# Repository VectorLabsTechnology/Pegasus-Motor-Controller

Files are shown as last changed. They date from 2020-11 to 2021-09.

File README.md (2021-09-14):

# Pegasus Motor Controller

## Objetivo

O objetivo do projeto é desenvolver um inversor para um motor síncrono de ímãs permanentes utilizando a técnica de controle orientado a campo. Com isso, se espera obter a familiaridadee com tecnologias modernas de controle de motores, tendo como objetivo final desenvolver um inversor capaz de acionar motores trifásicos e BLDC.

## Especificações

Em primeira instância, o motor a ser acionado será um motor oriundo de um _hoverboard_, brushless sensorado, operando a 48V e com potência máxima de 2,2kW. Com base nesses aprendizados, espera-se no futuro ser possível acionarmos um motor de maior tensão e potência, já de fabricação própria. As especificações técnicas mais específicas podem ser encontradas na [CT-001](/docs/CT-001-Especificacoes-Gerais.md).

## Organização do projeto

O repositório está dividido em quatro subdiretórios, `docs`, `fw`, `hw` e `sw`, que contêm respectivamente a documentação, firmware, hardware e software do projeto.
A parte de documentação é organizada majoritariamente no formato de [CTs](/docs/README.md). O design de hardware está sendo realizado com a ferramenta KiCad.

## Renders of the borads
Power Electronics:
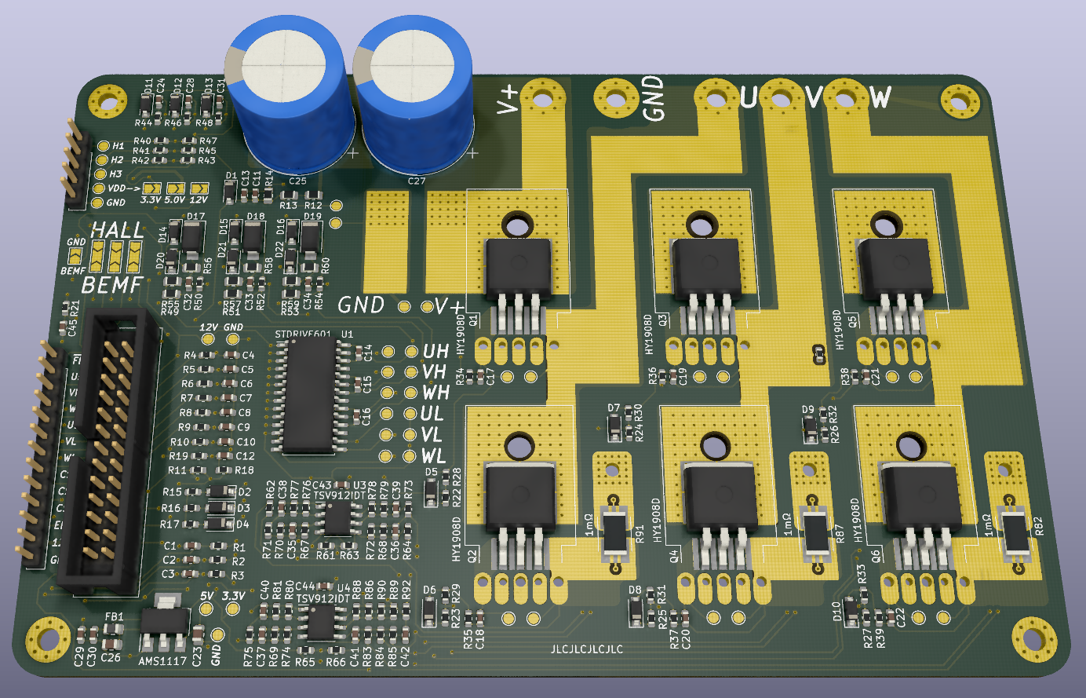
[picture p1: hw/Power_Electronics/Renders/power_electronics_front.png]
Power Electronics 1


Control Board:
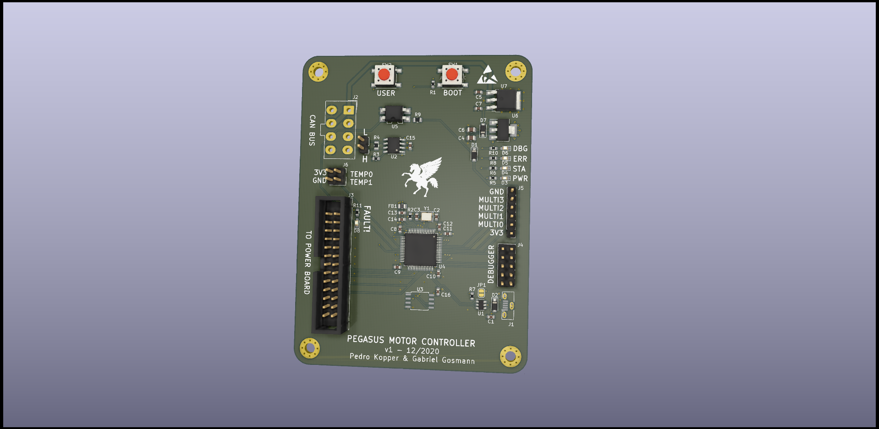
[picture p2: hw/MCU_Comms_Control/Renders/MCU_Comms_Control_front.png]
Control


Video of the test on a 3-phase induction motor
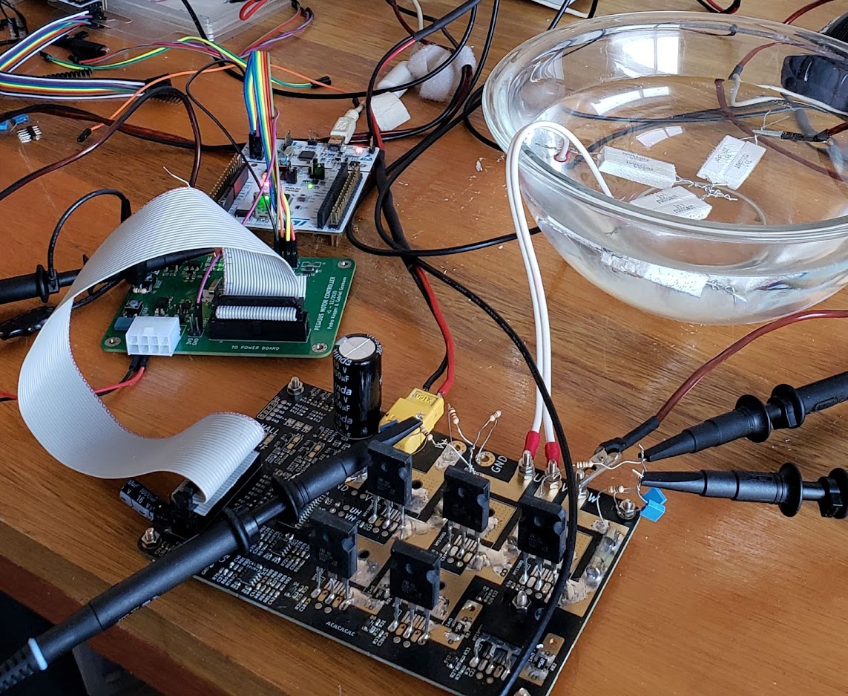
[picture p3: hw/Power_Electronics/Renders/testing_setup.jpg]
Watch the video (https://www.youtube.com/watch?v=kWv3p37wL9I&t=134s)


### Licença

O projeto está licenciado sob a licença MIT. Isso quer dizer que você tem o direto de reproduzir ele, tanto o software quanto o hardware.

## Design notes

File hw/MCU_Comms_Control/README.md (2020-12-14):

# Placa de controle

---

Placa renderizada frente

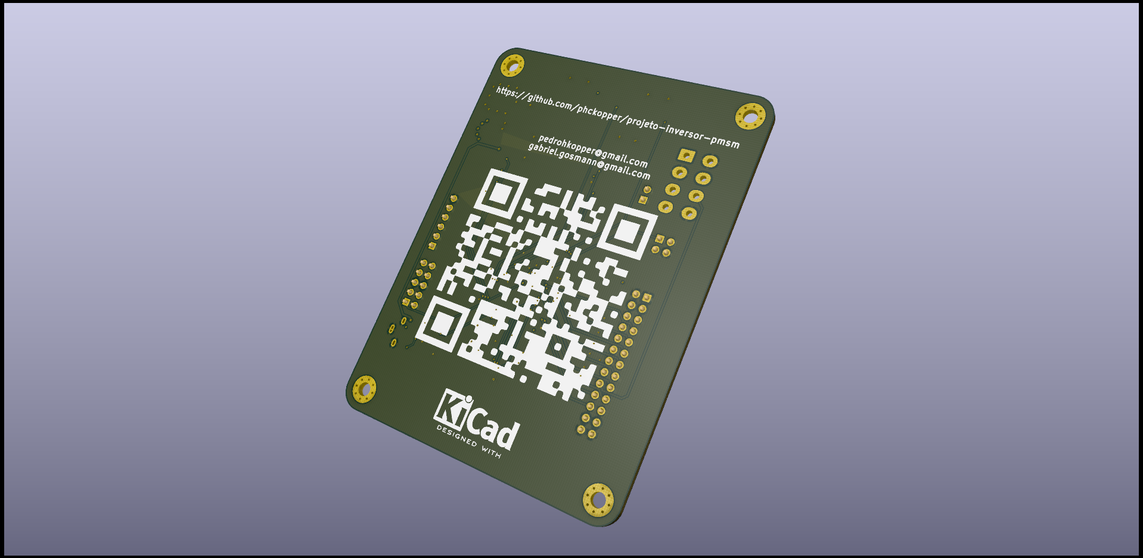
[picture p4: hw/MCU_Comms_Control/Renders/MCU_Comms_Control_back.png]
Placa renderizada trás


---

Essa placa é responsável por realizar o acionamento e controle dos motores. Utilizando um STM32F303, ela é capaz de medir a corrente ou força eletromotriz reversa de cada fase, possibilitando a comutação das bobinas. Além disso, possui entradas para sensores Hall, permitindo o uso de motores sensorados. 

Além do acionamento do motor, a placa realiza a comunicação com o resto do carro via barramento CAN, possibilitando o ajuste remoto de torque. Também possui uma entrada para o barramento de falha do carro, que desativa automaticamente a saída em caso de pane em qualquer um dos sistemas. Entradas para termistores permitem o monitoramento contínuo da temperatura da ponte do inversor, possibilitando o desarme em caso de sobreaquecimento. O monitoramento da tensão da bateria permite que as saídas sejam desligadas em caso de sobre/subtensão.

Com fim de telemetria, a placa conta com uma memória flash de 128Mbits, que pode ser lida através de conexão USB para possibilitar a caracterização da performance do inveersor e do motor, diagnosticar panes, entre outros.

---

Esse design é hardware livre e é disponibilizado através da licença CERN-OHL-S v2 (fortemente recíproca), disponível em inglês [aqui](https://ohwr.org/cern_ohl_s_v2.txt).

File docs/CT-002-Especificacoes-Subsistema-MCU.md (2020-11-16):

# [CT-001] Especificações do subsistema microcontrolado

**Escopo:** MCU e demais partes do controle eletrônico
**Objetivo:** Detalhar as especificações e a escolha dos componentes para a parte de controle microeletrônico

### Das especificações

O sistema microcontrolado deverá ser capaz de:

- [ ] Executar o algoritmo de controle orientado a campo especificado na [CT-001](/docs/CT-001-Especificacoes-Gerais.md) na frequência especificada, preferencialmente com o uso de uma FPU
- [ ] Realizar a amostragem do sinal das três correntes com frequência igual ou superior à frequência do algoritmo de controle orientado a campo, com a maior resolução possível
- [ ] Emitir seis saídas PWM, sendo elas três pares complementares, com frequência de chaveamento igual ou superior à especificada na CT-001.
- [ ] Ler três sensores de efeito Hall digitais com velocidade compatível com a especificação
- [ ] Possuir, preferencialmente, periférico CAN integrado suportando a especificação 2.0B a uma velocidade igual ou superior a 500kbps
- [ ] Possuir, preferencialmente, periférico SPI para possibilitar a adição da memória flash
- [ ] Possuir, preferencialmente, periférico USB para possibilitar uma interface de configuração e atualização de firmware em campo

### Das escolhas

Para cumprir as especificações anteriores, iniciamos pesquisando microcontroladores da fabricante ST, patrocinadora da e-Power e de conhecimento dos autores. Nisso, limitamos nosso espaço de escolha para a linha STM32.

Dentro das linhas STM32, existem diversas linhas, mas focaremos nas G0, G4, F0, F1 e F3, que são as consideradas para uso "mainstream". Dentre elas, a linha G é a mais recente, porém por conta disso possui disponibilidade muito limitada no mercado chinês no momento da escrita desse documento. Ficamos então com as linhas F1 e F3. Dentre elas, escolhemos a linha F3 por dois motivos principais:

* Impossibilidade de utilizar o periférico CAN ao mesmo tempo que o USB na linha F1, devido ao compartilhamento da SRAM
* Maior disponibilidade de periféricos analógicos na linha F3 (comparadores rápidos e amplificadores operacionais)

Dentro da linha F3, optamos pelo STM32F303 pois era o microcontrolador com maior disponibilidade e menor custo na LCSC/JLCPCB em novembro/2020. [Datasheet](https://www.st.com/resource/en/datasheet/stm32f303cc.pdf). O encapsulamento e número de pinos será estabelecido próximo ao término do design, porém os passos iniciais serão dados com a versão LQFP48.

### Do processamento

O STM32F303 é implementado em cima da arquitetura ARM Cortex-M4, voltada para alta performance e com suporte a ponto flutuante em hardware, o que facilita a escrita do algoritmo. Além disso, possui um controlador DMA de 12 canais, permitindo realizar diversas operações de movimentação de dados sem utilizar a CPU. Também possui uma MPU, que pode ser interessante para aumentar a segurança do firmware.

### Do conversor analógico digital (ADC)

O STM32F303 possui quatro ADCs, capazes de operar até 5Msps e multiplexados em até 39 canais, dependendo do encapsulamento escolhido. Sua resolução é programável até 12 bits e possibilita amostragem de 0V a 3.6V. Além disso, possui quatro PGAs integrados que possibilitam um ganho de 2x, 4x, 8x ou 16x, com entrada e saída rail-to-rail e largura de banda de 8.2MHz.

### Dos timers de controle do motor

O STM32F303 possui dois timers avançados (TIM1 e TIM8) que podem ser utilizados como PWM trifásico multiplexado em seis canais, com saídas complementares e dead-time programável. Esses timers também podem funcionar em conjunto com outros para realizar a sincronização de eventos dentro da MCU, por exemplo, de amostragem do conversor ADC.

### Das entradas de efeito Hall

O STM32F303 possui até 87 pinos de GPIO, sendo eles tolerantes a entradas de 5V, mesmo quando operando com Vcc = 3.3V. Todos eles são mapeados em vetores de interrupção externos e alguns podem ser conectados à timers para decodificação em quadratura via hardware.

### Do periférico CAN

O STM32F303 possui um periférico CAN que adere à espeecificação CAN2.0B e suporta velocidades de até 1Mbps e endereçamento de 29 bits.

### Do periférico SPI

O STM32F303 possui um periférico SPI que pode ser utilizado para interfacear tanto com memória flash quanto com cartões SD

### Do periférico USB

O STM32F303 possui um periférico USB compatível com a especificação full-speed (12Mbps), com SRAM dedicada para os buffers de transmissão e recepção. Para seu uso é necessário utilizar um cristal externo a partir do HSE.

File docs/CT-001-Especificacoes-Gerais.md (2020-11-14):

# [CT-001] Especificações gerais do projeto

**Escopo:** Todos subsistemas
**Objetivo:** Detalhar de maneira granular as especificações que devem ser cumpridas pelo projeto.

### Da etapa de potência

Deve ser capaz de:

- [ ] Ser alimentada por uma tensão de 36V a 48V
- [ ] Suportar uma corrente de 50A em regime contínuo
- [ ] Ser tolerante à picos de 150% do regime contínuo
- [ ] Desarmar caso uma sobrecorrente de 150% aconteça, só podedendo ser rearmado manualmente via botão ou CAN
- [ ] Permitir a leitura da corrente de pelo menos três fases separadamente
- [ ] Permitir a leitura da tensão de cada fase individualmente
- [ ] Permitir a leitura da tensão de alimentação
- [ ] Permitir a leitura da temperatura média dos MOSFETs da ponte
- [ ] Permitir um chaveamento de, no mínimo, 20 kHz

### Da parte microcontrolada

Deve ser capaz de:

- [ ] Ser alimentado através de uma fonte externa de 5V-24V
- [ ] Operar a partir de um barramento de 3.3V
- [ ] Consumir, no máximo, 100mA
- [ ] Medir a corrente das fases disponíveis e calcular as demais via software
- [ ] Realizar o controle orientado a campo das saídas
- [ ] Estimar a posição do rotor através de três entradas para sensores de efeito Hall
- [ ] Possuir saídas PWM capazes de acionar os gate drivers
- [ ] Monitorar condições de falha da etapa de potência, entrando em modo de erro caso necessário (sobrecorrente, sobretemperatura e violação das Leis de Kirchoff)
- [ ] Receber comandos de setpoint do torque via barramento CAN
- [ ] Responder, quando indagado via CAN, a velocidade, a corrente e a tensão do motor
- [ ] Armazenar em memória flash continuamente os parâmetros operacionais do motor, bem como o estado do software

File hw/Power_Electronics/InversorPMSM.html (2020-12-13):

# /home/phckopper/Projects/projeto-inversor-pmsm/hw/Power_Electronics/InversorPMSM.sch

sex 04 dez 2020 16:39:09

Eeschema 5.1.6

Component Count:178

Ref | Qnty | Value | Part | Datasheet | Description | Vendor
C1, C2, C3, C4, C5, C6, C32, C33, C34, C38 | 10 | 33pF | Device:C | Samsung-Electro-Mechanics-CL10C330JB8NNNC_C1663.pdf | Unpolarized capacitor
C7, C8, C26, C27, C40, C41 | 6 | 100nF | Device:C | ~ | Unpolarized capacitor
C9, C13, C14, C15, C16, C17, C18 | 7 | DNM | Device:C | | Unpolarized capacitor
C10, C11, C12 | 3 | 470nF | Device:C | Samsung-Electro-Mechanics-CL10B474KA8NNNC_C1623.pdf | Unpolarized capacitor
C19, C22 | 2 | 22uF | Device:C | ~ | Unpolarized capacitor
C20, C25, C28, C29, C30, C31, C35, C36, C37 | 9 | 10pF | Device:C | Samsung-Electro-Mechanics-CL10C330JB8NNNC_C1663.pdf | Unpolarized capacitor
C21 | 1 | CP | Device:CP | ~ | Polarized capacitor
C23 | 1 | CP | Device:CP | ~ | Polarized capacitor
C24 | 1 | DNM | Device:C | ~ | Unpolarized capacitor
C39 | 1 | 1nF | Device:C | ~ | Unpolarized capacitor
D1, D5, D6, D7, D8, D9, D10, D11, D12, D13, D14, D15, D16, D20, D21, D22 | 16 | B5819W | Device:D_Schottky | Changjiang-Electronics-Tech-CJ-B5819W_C8598.pdf | Schottky diode
D2, D3, D4 | 3 | DNM | Device:D_Schottky | | Schottky diode
D17, D18, D19 | 3 | RS1J | Device:D | ~ | Diode
FB1 | 1 | Ferrite | Device:Ferrite_Bead | ~ | Ferrite bead
H1, H2, H3, H4 | 4 | MountingHole_Pad | Mechanical:MountingHole_Pad | ~ | Mounting Hole with connection
J1 | 1 | FROM_CONTROL_BOARD | Connector_Generic:Conn_02x13_Odd_Even | ~ | Generic connector, double row, 02x13, odd/even pin numbering scheme (row 1 odd numbers, row 2 even numbers), script generated (kicad-library-utils/schlib/autogen/connector/)
J2 | 1 | HALL_CONNECTOR | Connector:Conn_01x05_Male | ~ | Generic connector, single row, 01x05, script generated (kicad-library-utils/schlib/autogen/connector/)
J3 | 1 | POWER_INPUT | Connector:Screw_Terminal_01x02 | ~ | Generic screw terminal, single row, 01x02, script generated (kicad-library-utils/schlib/autogen/connector/)
J4 | 1 | OUTPUT POWER | Connector:Screw_Terminal_01x03 | ~ | Generic screw terminal, single row, 01x03, script generated (kicad-library-utils/schlib/autogen/connector/)
JP1, JP2, JP3 | 3 | Jumper_2_Open | Jumper:Jumper_2_Open | ~ | Jumper, 2-pole, open
JP4, JP5, JP6 | 3 | Jumper_3_Open | Jumper:Jumper_3_Open | ~ | Jumper, 3-pole, both open
Q1, Q2, Q3, Q4, Q5, Q6 | 6 | HY1908D | Transistor_FET:IRF3205 | https://datasheet.lcsc.com/szlcsc/1809071509_HUAYI-HY1908D_C108891.pdf | 110A Id, 55V Vds, Single N-Channel HEXFET Power MOSFET, 8mOhm Ron, TO-220AB
Q7, Q8, Q9, Q10, Q11, Q12 | 6 | JCS24N50WH | Transistor_FET:IRF3205 | | 110A Id, 55V Vds, Single N-Channel HEXFET Power MOSFET, 8mOhm Ron, TO-220AB
R1, R2, R3, R4, R5, R6, R42, R44, R46, R75, R76, R77, R78 | 13 | 1K | Device:R | Uniroyal-Elec-0603WAF1001T5E_C21190.pdf | Resistor
R7, R26, R27, R28, R29, R30, R31, R53, R55, R57, R59, R60, R61, R68, R69, R70, R71, R72, R73 | 19 | 100K | Device:R | Uniroyal-Elec-0603WAF1003T5E_C25803.pdf | Resistor
R8, R9, R41, R43, R45, R47, R49, R51 | 8 | 100K | Device:R | | Resistor
R10, R48, R50, R52 | 4 | 5.6K | Device:R | | Resistor
R11, R12, R13 | 3 | 27R | Device:R | | Resistor
R14, R15, R16, R17, R18, R19 | 6 | 10R | Device:R | https://datasheet.lcsc.com/szlcsc/Uniroyal-Elec-0603WAF100JT5E_C22859.pdf | Resistor
R20, R21, R22, R23, R24, R25 | 6 | 100R | Device:R | Uniroyal-Elec-0603WAF1000T5E_C22775.pdf | Resistor
R32, R33, R34, R54, R56, R58, R63, R65, R67 | 9 | 2K | Device:R | Uniroyal-Elec-0603WAF1001T5E_C21190.pdf | Resistor
R35, R37, R39, R84 | 4 | 10K | Device:R | | Resistor
R36, R38, R40, R62, R64, R66, R80, R82 | 8 | DNM | Device:R | Uniroyal-Elec-0603WAF1001T5E_C21190.pdf | Resistor
R74, R79, R83 | 3 | 1mΩ | Device:R | ~ | Resistor
R81 | 1 | 39K | Device:R | Uniroyal-Elec-0603WAF1003T5E_C25803.pdf | Resistor
U1 | 1 | STDRIVE601 | inversor-pmsm:STDRIVE601 | https://www.st.com/resource/en/datasheet/stdrive601.pdf | Triple half-bridge high-voltage gate driver
U2 | 1 | AMS1117 | Regulator_Linear:AMS1117 | http://www.advanced-monolithic.com/pdf/ds1117.pdf | 1A Low Dropout regulator, positive, adjustable output, SOT-223
U3, U4 | 2 | TSV912IDT | Amplifier_Operational:TSV912IDT | www.st.com/resource/en/datasheet/tsv911.pdf | Dual rail-to-rail input/output 8 MHz operational amplifiers, SOIC-8

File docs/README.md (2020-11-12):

# Documentação do projeto

Nesse diretório estão contidas as CTs (Considerações Técnicas) realizadas durante o desenvolvimento do projeto. O objetivo delas é documentar o processo decisório realizado durante o design do inversor, e não somente o resultado final.

As CTs devem ser escrita no formato Markdown (.md) e seguir o seguinte formato:

```
# [CT-xxx] [Título descritivo (eg. Estimação da dissipação de potência nos MOSFETs)]

*Escopo:* [Quais subsistemas são considerados nessa CT (eg. MOSFETs da ponte)]
*Objetivo:* [Descrever de maneira mais precisa o conteúdo da CT]

[Corpo]
```

O objetivo de adotar o sistema de CTs é permitir que as decisões de design sejam documentadas de maneira consistente e, assim, o projeto se torne verificável por terceiros e facilite a inclusão de novos membros na equipe, além de facilitar o surgimento de adaptações e outros trabalhos derivativos.

O link entre CTs é encorajado e, sempre que for possível, tente linkar no corpo para as CTs que contém as informações que você referencia.

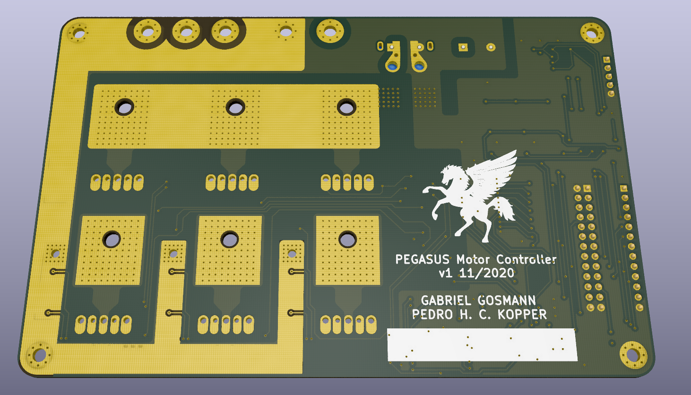
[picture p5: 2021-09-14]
hw/Power_Electronics/Renders/power_electronics_back.png

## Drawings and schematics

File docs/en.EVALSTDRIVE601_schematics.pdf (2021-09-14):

### HIGH VOLTAGE SECTION

### VCC_E min 9V max 20V

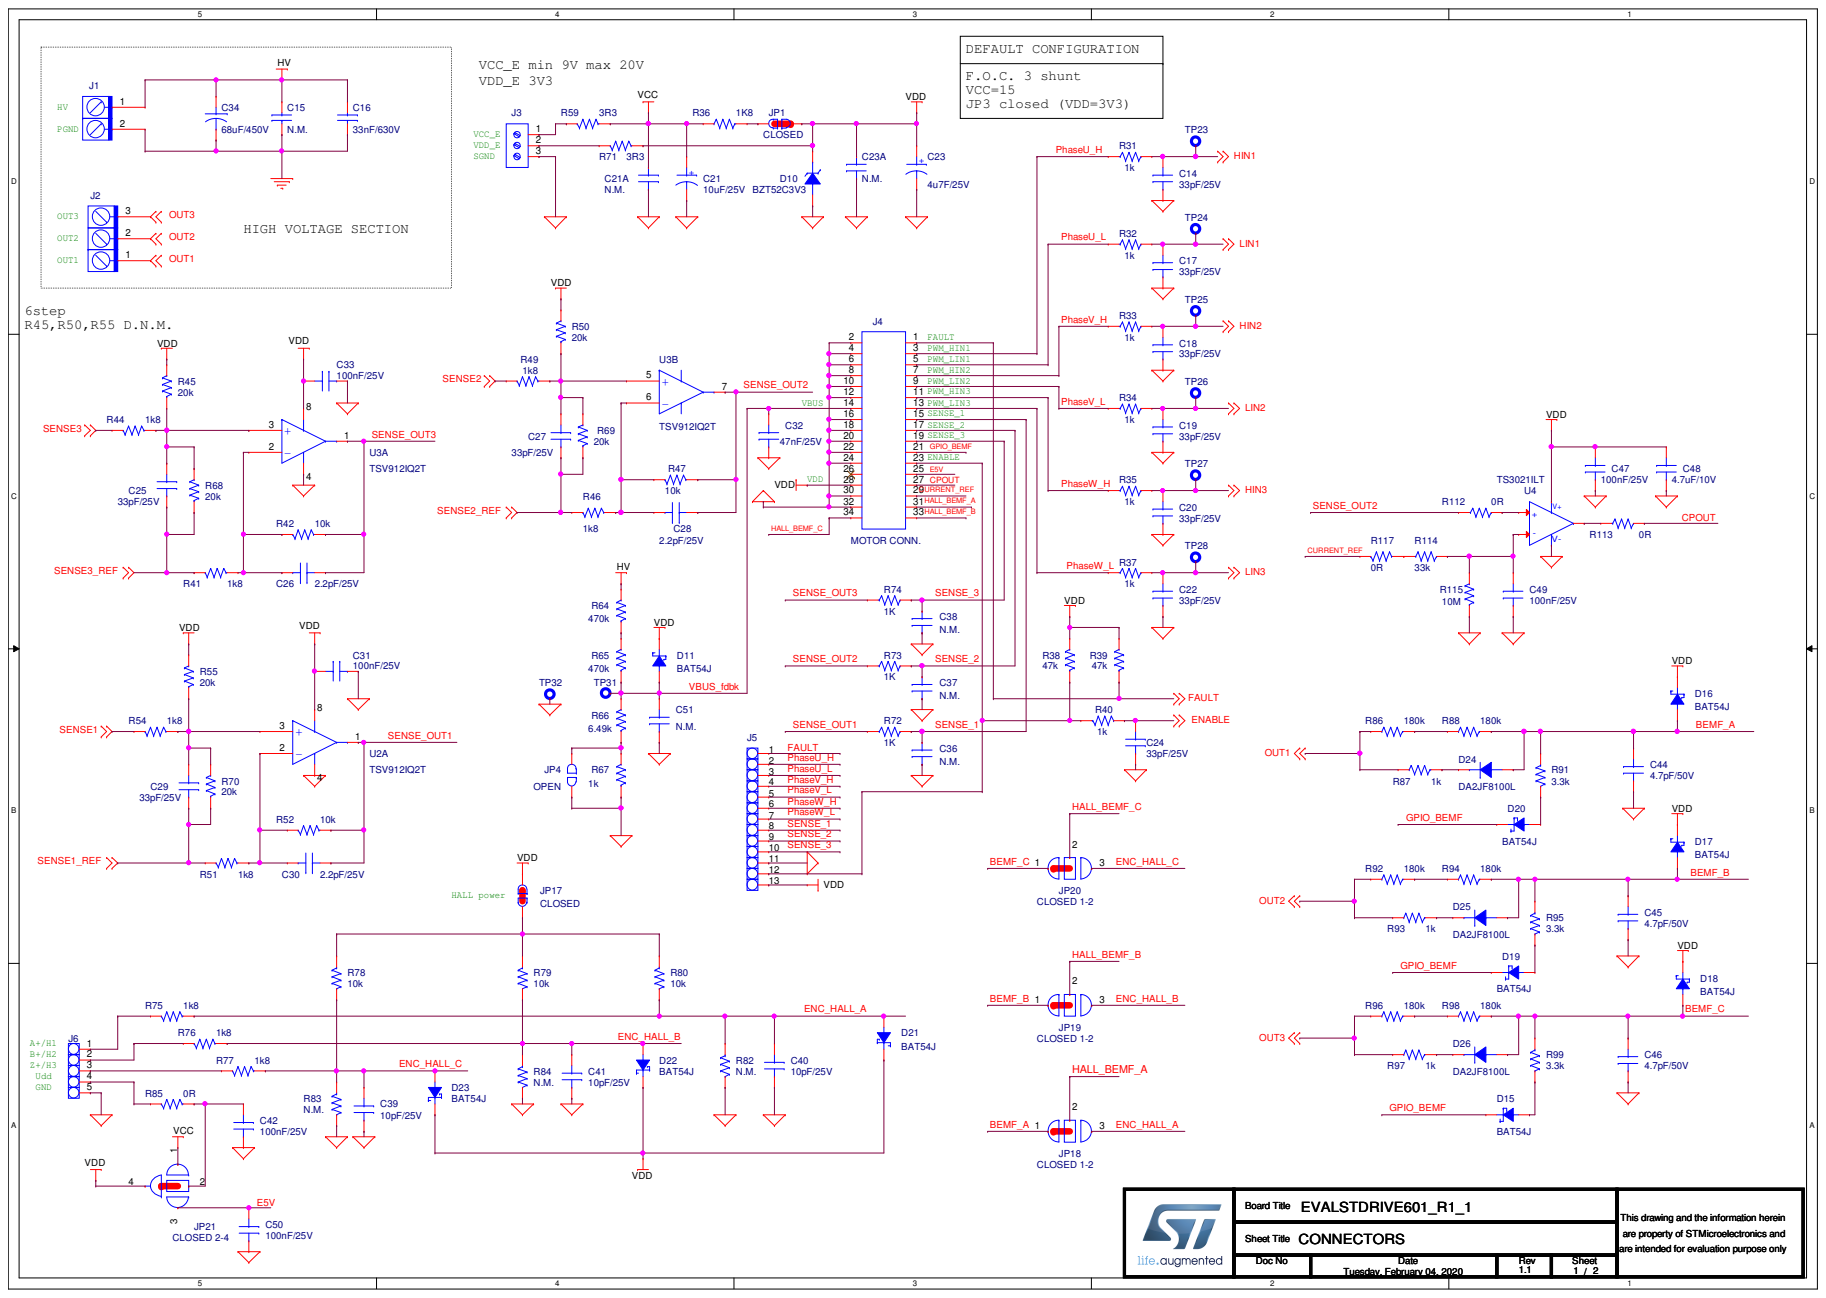
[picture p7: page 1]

This drawing and the information herein
are property of STMicroelectronics and
are intended for evaluation purpose only

HV

SGND | PGND

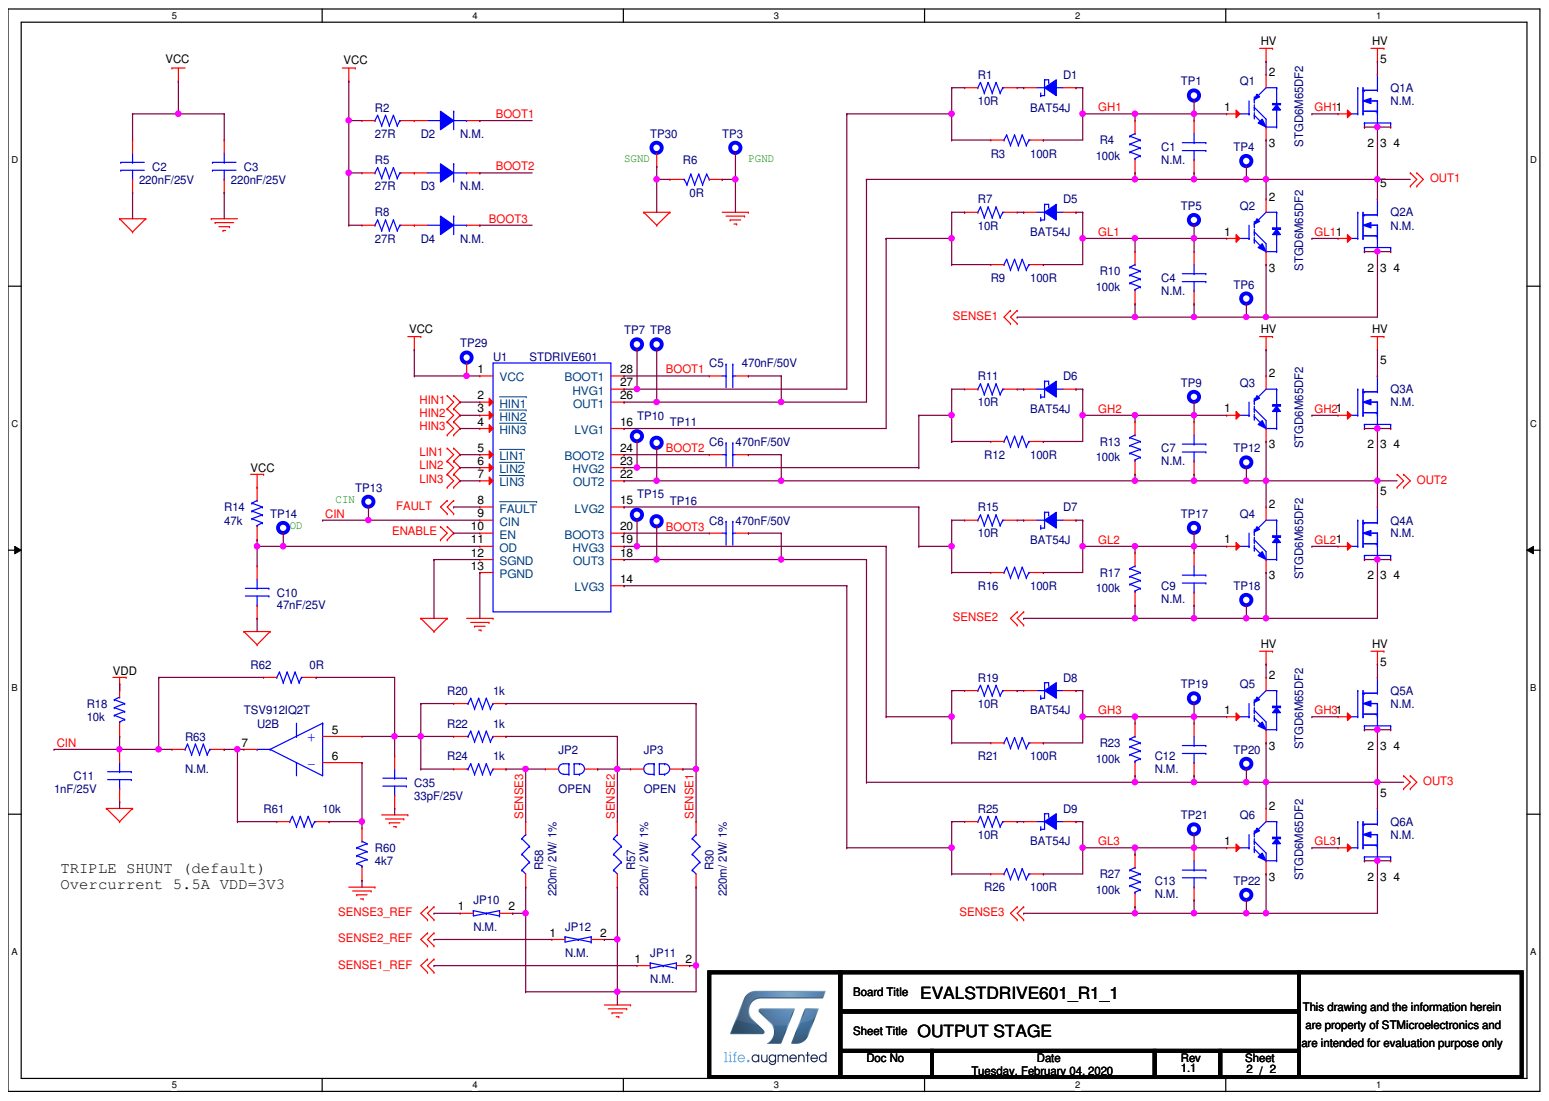
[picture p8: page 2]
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

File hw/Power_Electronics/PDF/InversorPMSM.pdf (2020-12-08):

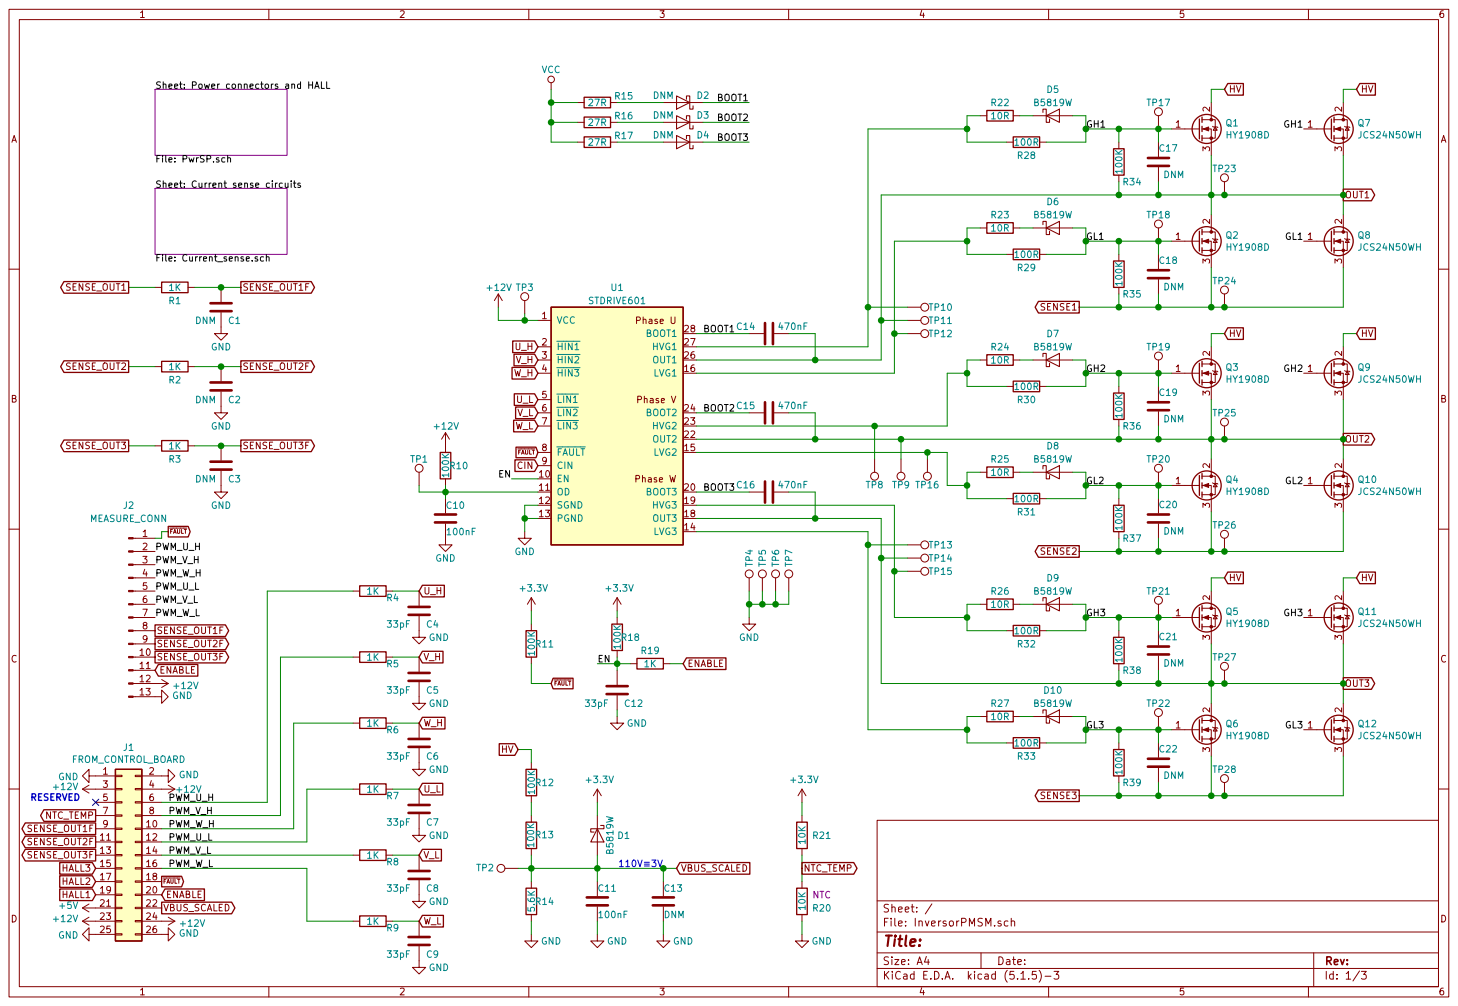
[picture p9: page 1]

Sheet: Power connectors and HALL File: PwrSP.sch Sheet: Current sense circuits File: Current_sense.sch

Id: 1/3 Title: File: InversorPMSM.sch Sheet: /

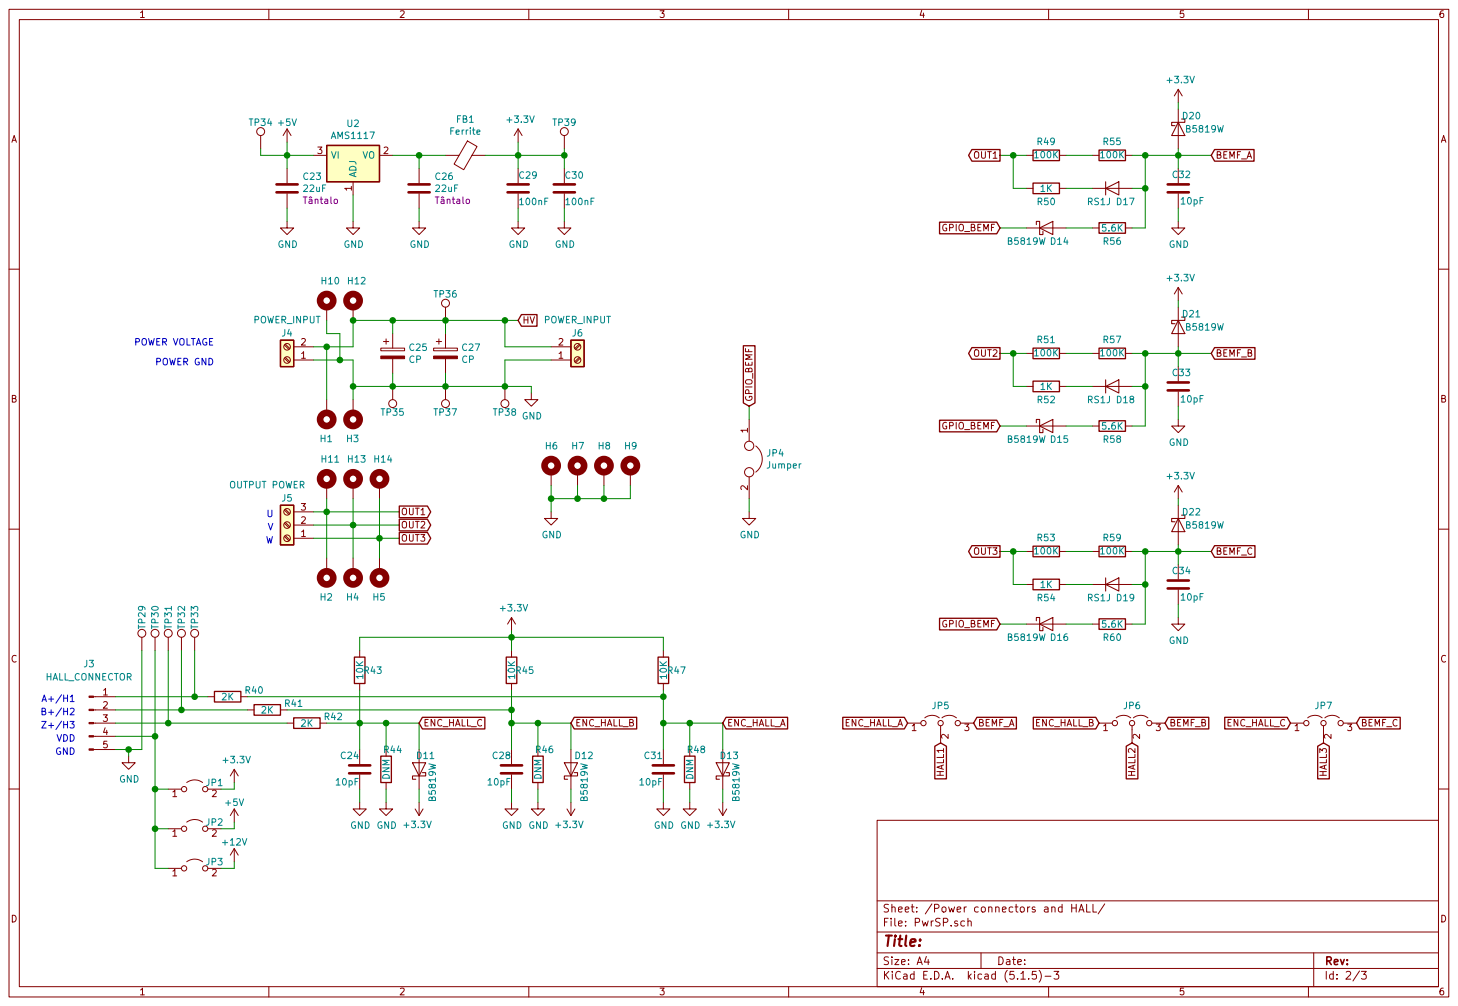
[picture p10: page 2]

Id: 2/3 Title: File: PwrSP.sch Sheet: /Power connectors and HALL/ +12V

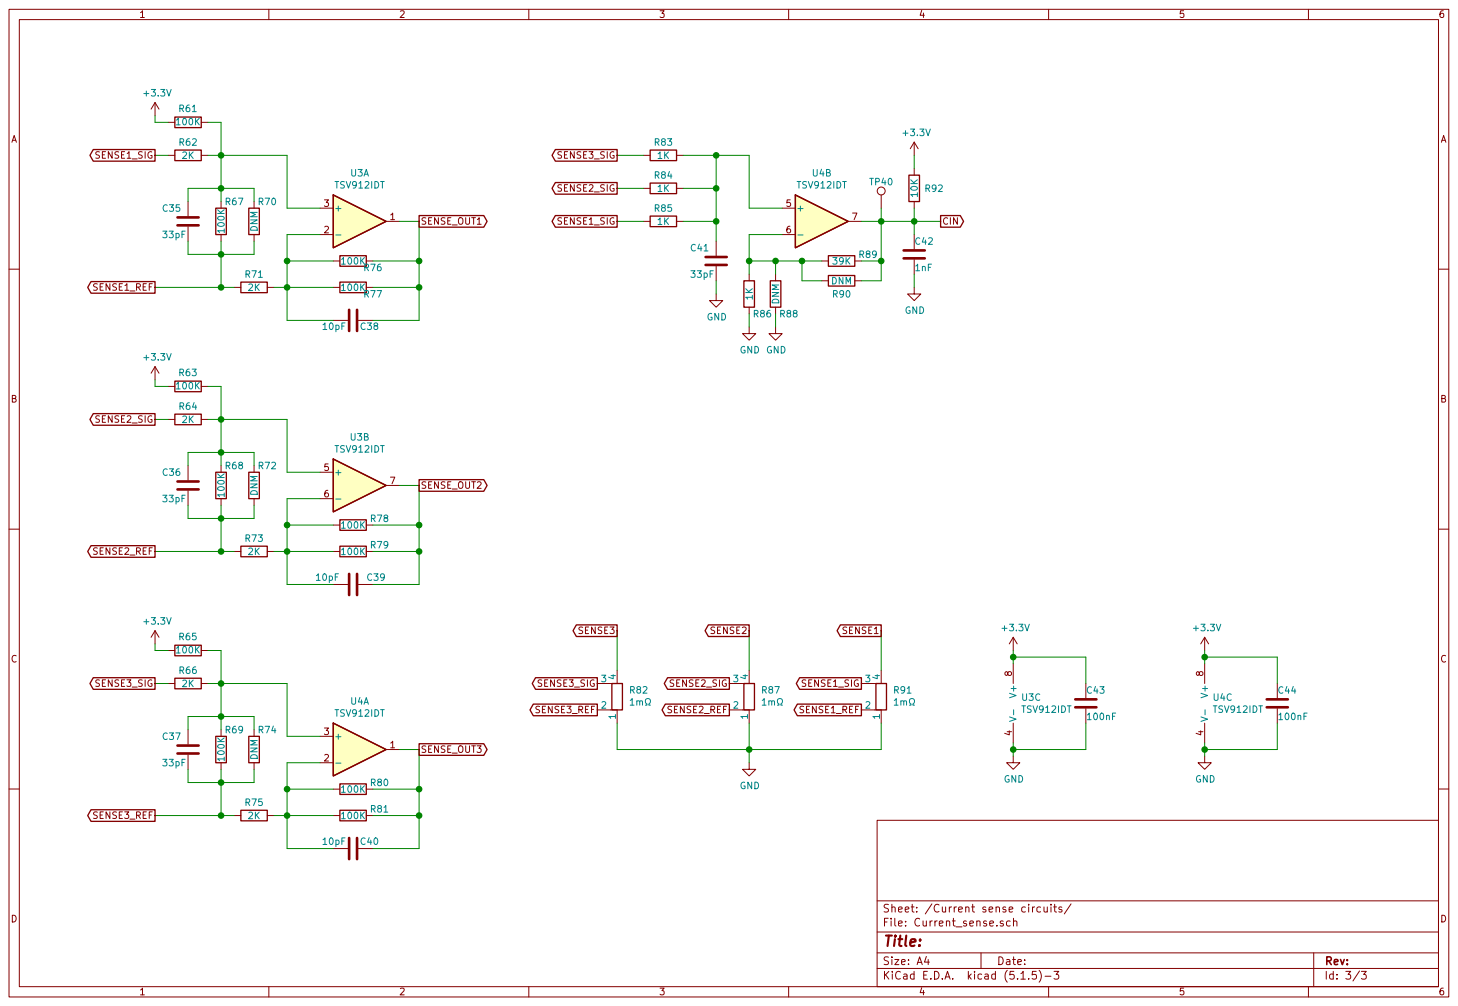
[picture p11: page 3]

File: Current_sense.sch Sheet: /Current sense circuits/ R72 DNM

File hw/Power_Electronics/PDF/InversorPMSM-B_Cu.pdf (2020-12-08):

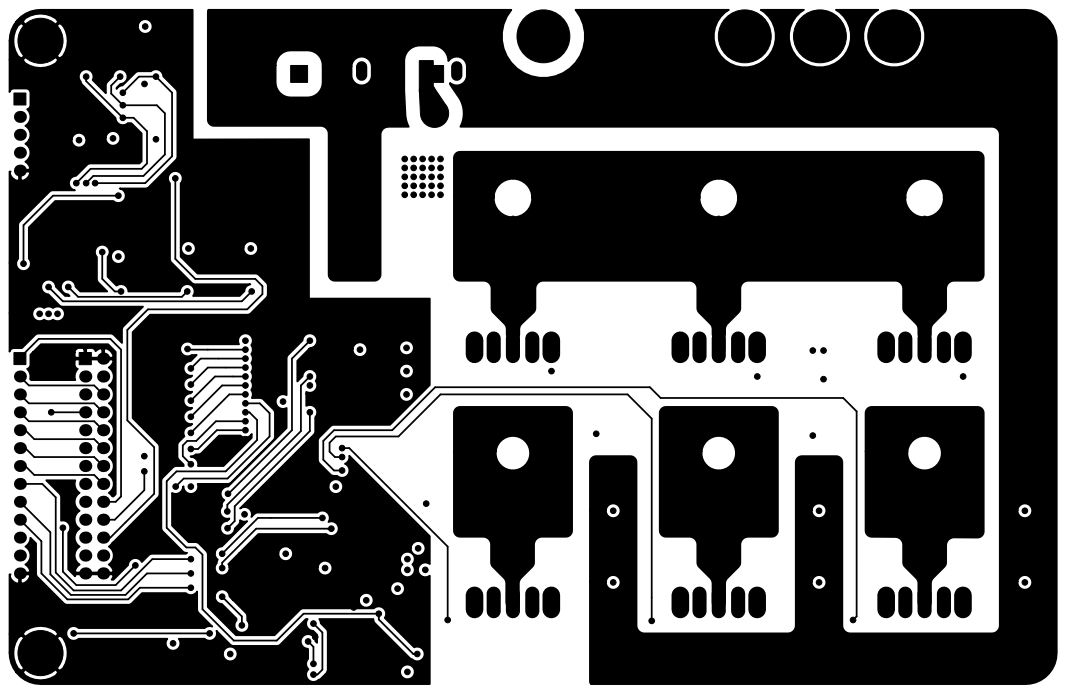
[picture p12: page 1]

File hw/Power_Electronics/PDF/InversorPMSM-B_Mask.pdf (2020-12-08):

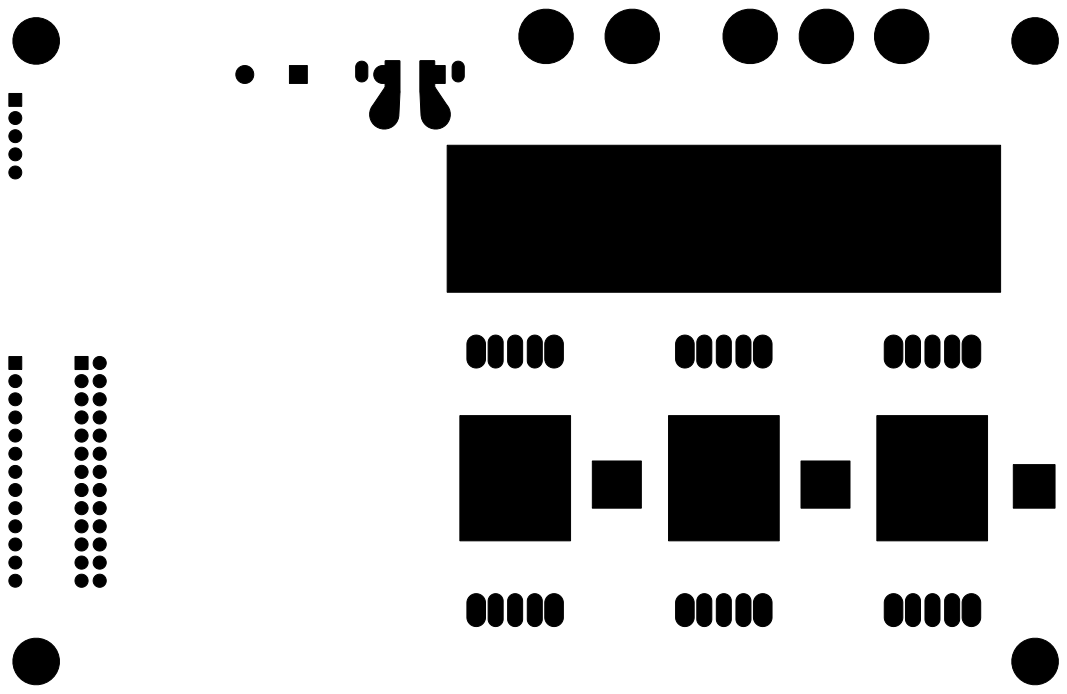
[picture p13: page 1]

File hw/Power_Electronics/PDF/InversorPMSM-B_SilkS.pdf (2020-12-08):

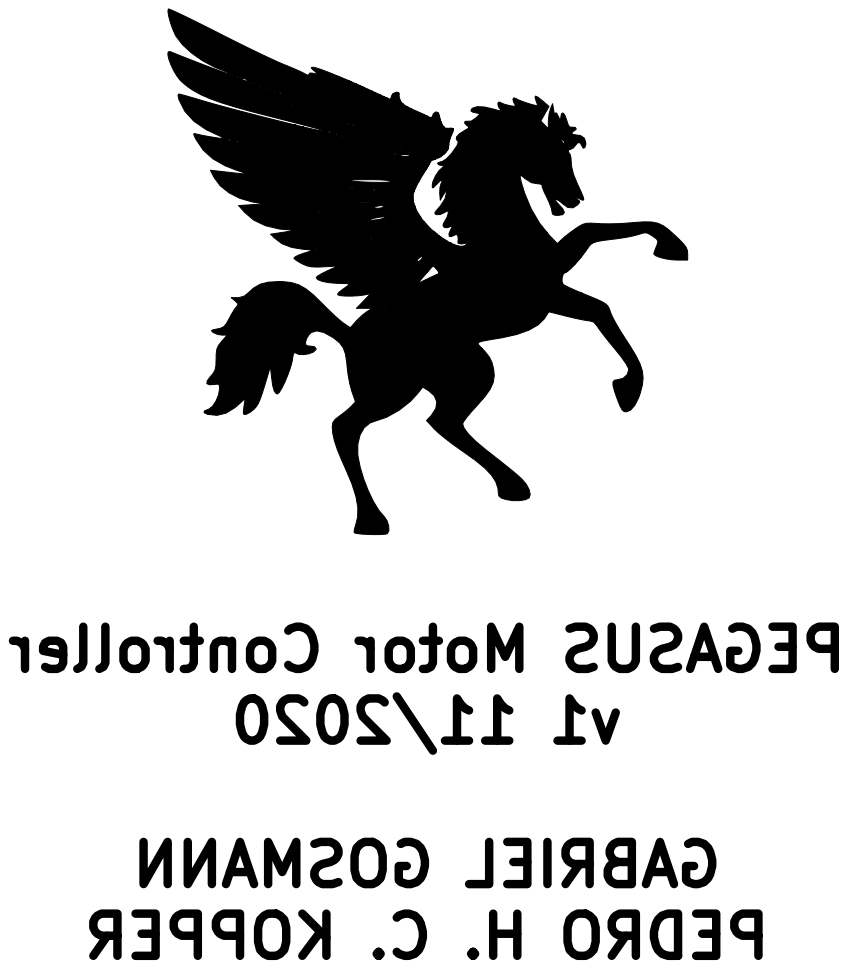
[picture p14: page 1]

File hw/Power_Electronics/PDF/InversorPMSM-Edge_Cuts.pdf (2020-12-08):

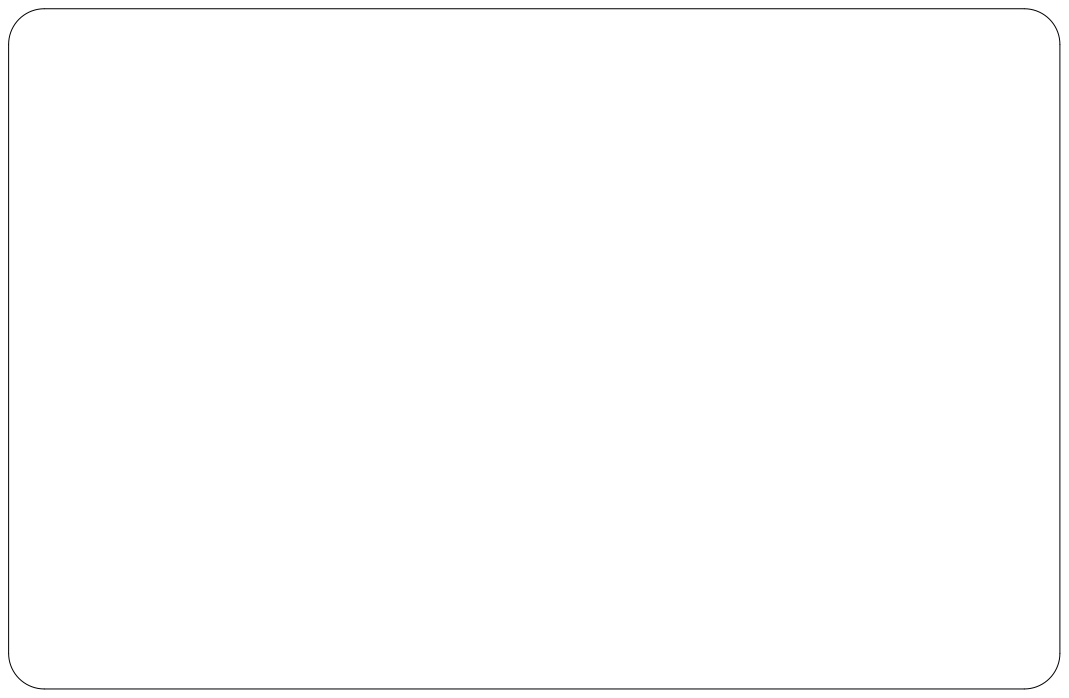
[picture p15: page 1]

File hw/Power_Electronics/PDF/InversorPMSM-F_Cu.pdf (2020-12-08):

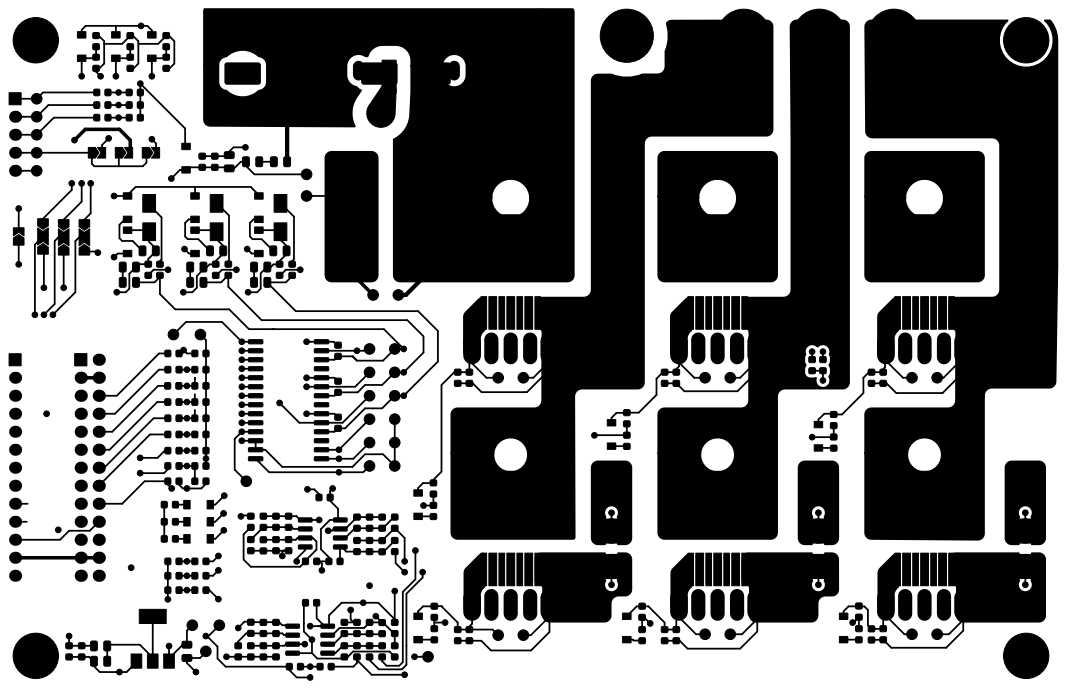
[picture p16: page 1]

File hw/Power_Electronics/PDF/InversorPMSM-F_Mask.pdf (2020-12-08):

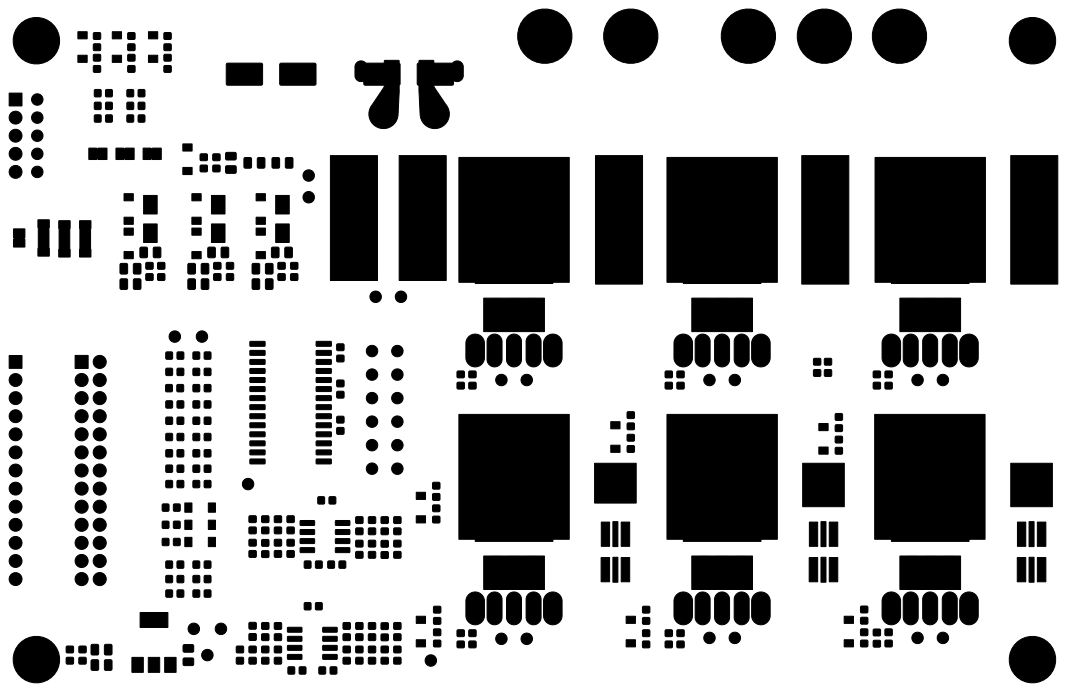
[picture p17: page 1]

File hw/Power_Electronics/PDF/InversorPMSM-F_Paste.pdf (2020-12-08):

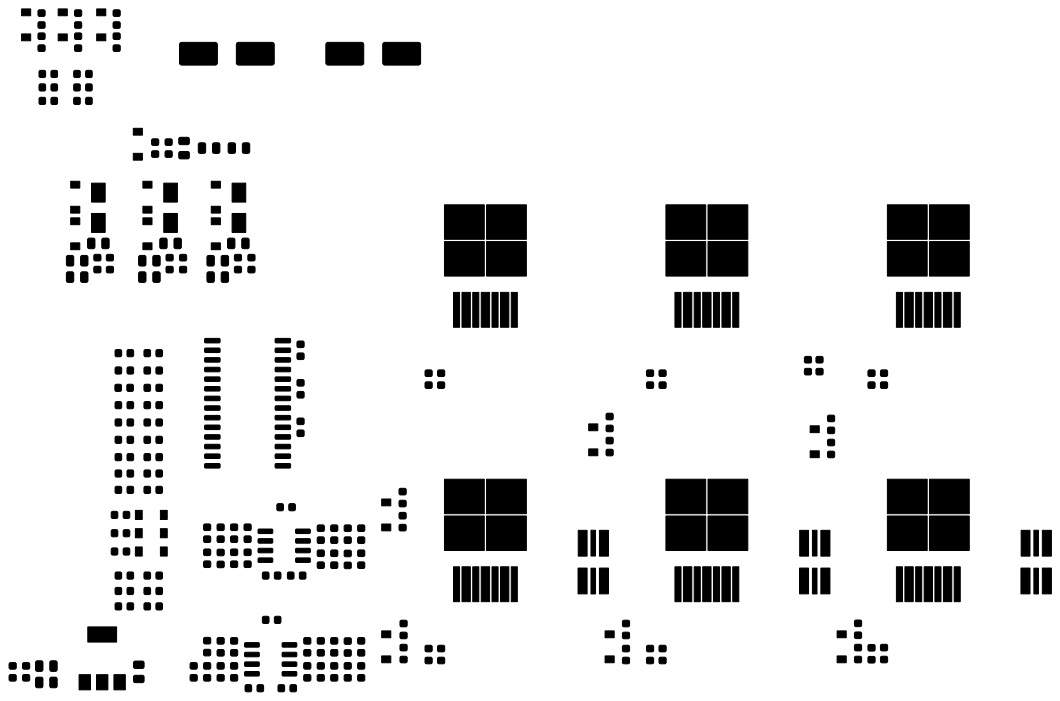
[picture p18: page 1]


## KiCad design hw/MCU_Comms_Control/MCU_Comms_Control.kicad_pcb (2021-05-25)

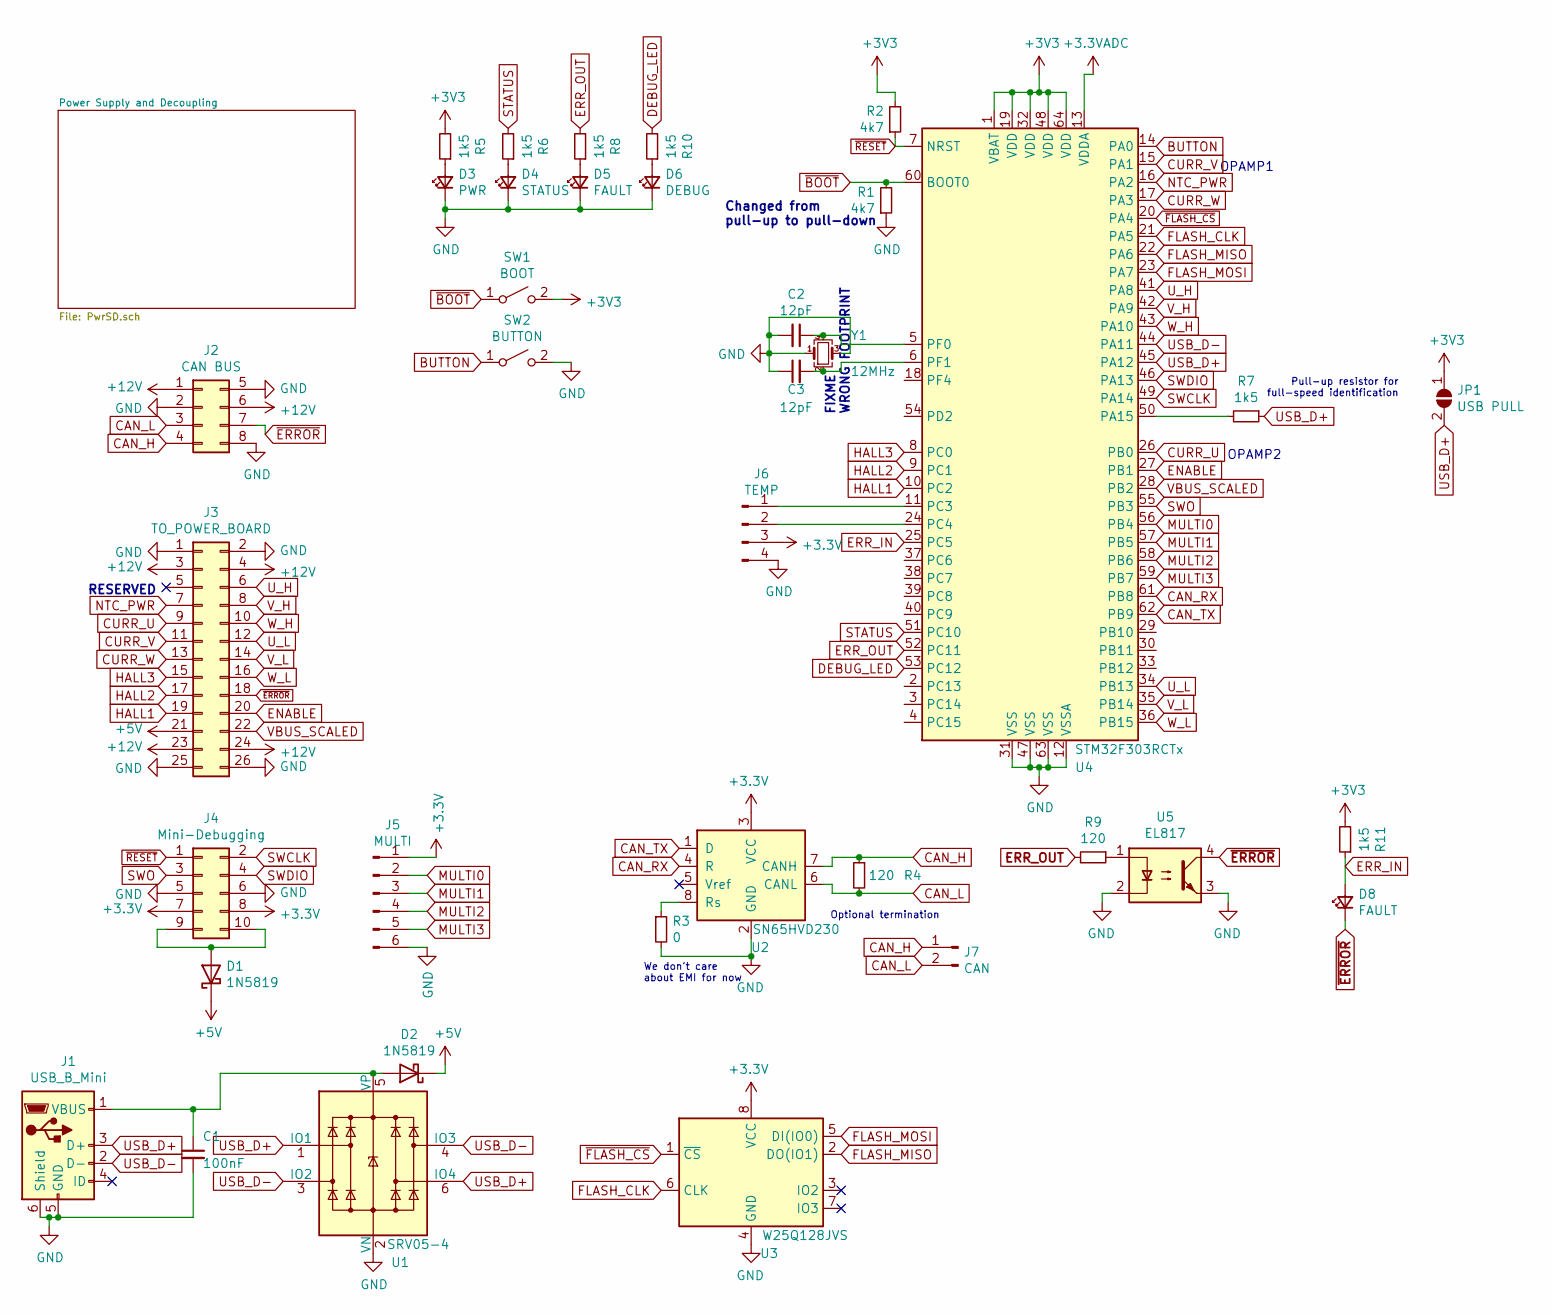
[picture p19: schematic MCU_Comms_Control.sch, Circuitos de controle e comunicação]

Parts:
C1: 100nF; C_0603_1608Metric; LCSC C14663
C2, C3: 12pF; C_0603_1608Metric; LCSC C38523
D1, D2: 1N5819; D_SOD-123; LCSC C8598
D3: PWR; LED_0603_1608Metric_Castellated; LCSC C72043
D4: STATUS; LED_0603_1608Metric_Castellated; LCSC C72041
D5, D8: FAULT; LED_0603_1608Metric_Castellated; LCSC C2286
D6: DEBUG; LED_0603_1608Metric_Castellated; LCSC C72041
J1: USB_B_Mini; USB_Micro-B_Molex-105133-0001
J2: CAN BUS; Molex_Mini-Fit_Jr_5566-08A_2x04_P4.20mm_Vertical
J3: TO_POWER_BOARD; IDC-Header_2x13_P2.54mm_Vertical
J4: Mini-Debugging; PinHeader_2x05_P2.54mm_Vertical
J5: MULTI; PinHeader_1x06_P2.54mm_Vertical
J6: TEMP; PinHeader_2x02_P2.54mm_Vertical
J7: CAN; PinHeader_1x02_P2.54mm_Vertical
JP1: USB PULL; SolderJumper-2_P1.3mm_Open_RoundedPad1.0x1.5mm
R1, R2: 4k7; R_0603_1608Metric; LCSC C23162
R3: 0; R_0603_1608Metric; LCSC C21189
R4, R9: 120; R_0805_2012Metric; LCSC C17437
R5, R6, R7, R8, R10, R11: 1k5; R_0603_1608Metric; LCSC C22843
SW1: BOOT; SW_SPST_PTS645
SW2: BUTTON; SW_SPST_PTS645
U1: SRV05-4; SOT-23-6; LCSC C85364
U2: SN65HVD230; SOIC-8_3.9x4.9mm_P1.27mm; LCSC C12084
U3: W25Q128JVS; SOIC-8_5.23x5.23mm_P1.27mm; LCSC C97521
U4: STM32F303RCTx; LQFP-64_10x10mm_P0.5mm
U5: EL817; SMDIP-4_W7.62mm; LCSC C106900
Y1: 12MHz; Crystal_SMD_3225-4Pin_3.2x2.5mm; LCSC C9002

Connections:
+3.3VADC: U4.13 (VDDA); also elsewhere on the board
+5V: D1.1 (K), D2.1 (K), J3.21; also elsewhere on the board
+12V: J2.1, J2.6, J3.3, J3.4, J3.23, J3.24; also elsewhere on the board
BUTTON: SW2.1 (A), U4.14 (PA0)
CAN_H: J2.4, J7.1, R4.1, U2.7 (CANH)
CAN_L: J2.3, J7.2, R4.2, U2.6 (CANL)
CAN_RX: U2.4 (R), U4.61 (PB8)
CAN_TX: U2.1 (D), U4.62 (PB9)
CURR_U: J3.9, U4.26 (PB0)
CURR_V: J3.11, U4.15 (PA1)
CURR_W: J3.13, U4.17 (PA3)
DEBUG_LED: R10.2, U4.53 (PC12)
ENABLE: J3.20, U4.27 (PB1)
ERR_IN: D8.2 (A), R11.1, U4.25 (PC5)
ERR_OUT: R8.2, R9.2, U4.52 (PC11)
FLASH_CLK: U3.6 (CLK), U4.21 (PA5)
FLASH_MISO: U3.2 (DO(IO1)), U4.22 (PA6)
FLASH_MOSI: U3.5 (DI(IO0)), U4.23 (PA7)
GND: C1.2, C2.2, C3.1, D3.1 (K), D4.1 (K), D5.1 (K), D6.1 (K), J1.5 (GND), J1.6 (Shield), J2.2, J2.5, J2.8, J3.1, J3.2, J3.25, J3.26, J4.5, J4.6, J5.6, J6.4, R1.1, R3.2, SW2.2 (B), U1.2 (VN), U2.2 (GND), U3.4 (GND), U4.12 (VSSA), U4.31 (VSS), U4.47 (VSS), U4.63 (VSS), U5.2, U5.3, Y1.1, Y1.3; also elsewhere on the board
HALL1: J3.19, U4.10 (PC2)
HALL2: J3.17, U4.9 (PC1)
HALL3: J3.15, U4.8 (PC0)
MULTI0: J5.2, U4.56 (PB4)
MULTI1: J5.3, U4.57 (PB5)
MULTI2: J5.4, U4.58 (PB6)
MULTI3: J5.5, U4.59 (PB7)
NTC_PWR: J3.7, U4.16 (PA2)
unnamed: C1.1, D2.2 (A), J1.1 (VBUS), U1.5 (VP)
unnamed: C2.1, U4.5 (PF0), Y1.4
unnamed: C3.2, U4.6 (PF1), Y1.2
unnamed: D1.2 (A), J4.9, J4.10
unnamed: D3.2 (A), R5.1
unnamed: D4.2 (A), R6.1
unnamed: D5.2 (A), R8.1
unnamed: D6.2 (A), R10.1
unnamed: J6.1, U4.11 (PC3)
unnamed: J6.2, U4.24 (PC4)
unnamed: R3.1, U2.8 (Rs)
unnamed: R7.2, U4.50 (PA15)
unnamed: R9.1, U5.1
STATUS: R6.2, U4.51 (PC10)
SWCLK: J4.2, U4.49 (PA14)
SWDIO: J4.4, U4.46 (PA13)
SWO: J4.3, U4.55 (PB3)
USB_D+: J1.3 (D+), JP1.2 (B), R7.1, U1.1 (IO1), U1.6 (IO4), U4.45 (PA12)
USB_D-: J1.2 (D-), U1.3 (IO2), U1.4 (IO3), U4.44 (PA11)
U_H: J3.6, U4.41 (PA8)
U_L: J3.12, U4.34 (PB13)
VBUS_SCALED: J3.22, U4.28 (PB2)
V_H: J3.8, U4.42 (PA9)
V_L: J3.14, U4.35 (PB14)
W_H: J3.10, U4.43 (PA10)
W_L: J3.16, U4.36 (PB15)
~BOOT: R1.2, SW1.1 (A), U4.60 (BOOT0)
~ERROR: D8.1 (K), J2.7, J3.18, U5.4
~FLASH_CS: U3.1 (~CS), U4.20 (PA4)
~RESET: J4.1, R2.1, U4.7 (NRST)

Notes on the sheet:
Optional termination
We don't care about EMI for now
Pull-up resistor for full-speed identification
RESERVED
OPAMP1
OPAMP2
Changed from pull-up to pull-down
FIXME WRONG FOOTPRINT

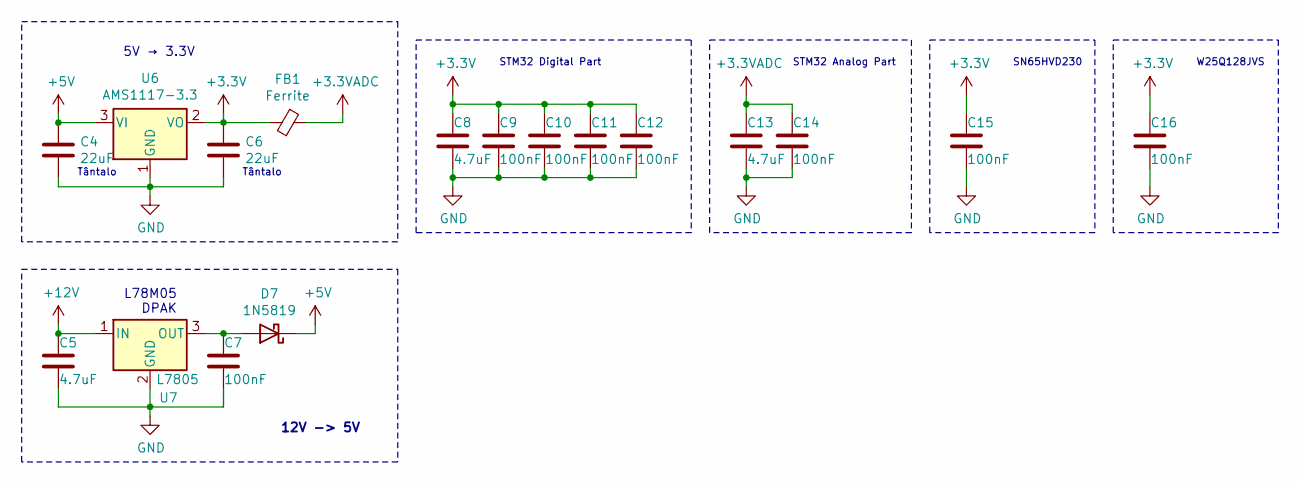
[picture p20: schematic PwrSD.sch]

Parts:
C4, C6: 22uF; C_0805_2012Metric; LCSC C45783
C5, C8, C13: 4.7uF; C_0603_1608Metric; LCSC C19666
C7, C9, C10, C11, C12, C14, C15, C16: 100nF; C_0603_1608Metric; LCSC C14663
D7: 1N5819; D_SOD-123; LCSC C8598
FB1: Ferrite; L_0805_2012Metric; LCSC e
U6: AMS1117-3.3; SOT-223-3_TabPin2; LCSC C6186
U7: L7805; TO-252-3_TabPin2; LCSC C58069

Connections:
+3.3VADC: C13.1, C14.1, FB1.1; also elsewhere on the board
+5V: C4.1, D7.1 (K), U6.3 (VI); also elsewhere on the board
+12V: C5.1, U7.1 (IN); also elsewhere on the board
GND: C4.2, C5.2, C6.2, C7.2, C8.2, C9.2, C10.2, C11.2, C12.2, C13.2, C14.2, C15.2, C16.2, U6.1 (GND), U7.2 (GND); also elsewhere on the board
unnamed: C7.1, D7.2 (A), U7.3 (OUT)

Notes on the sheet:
Tântalo
STM32 Digital Part
STM32 Analog Part
5V → 3.3V
SN65HVD230
W25Q128JVS
L78M05 DPAK
12V -> 5V

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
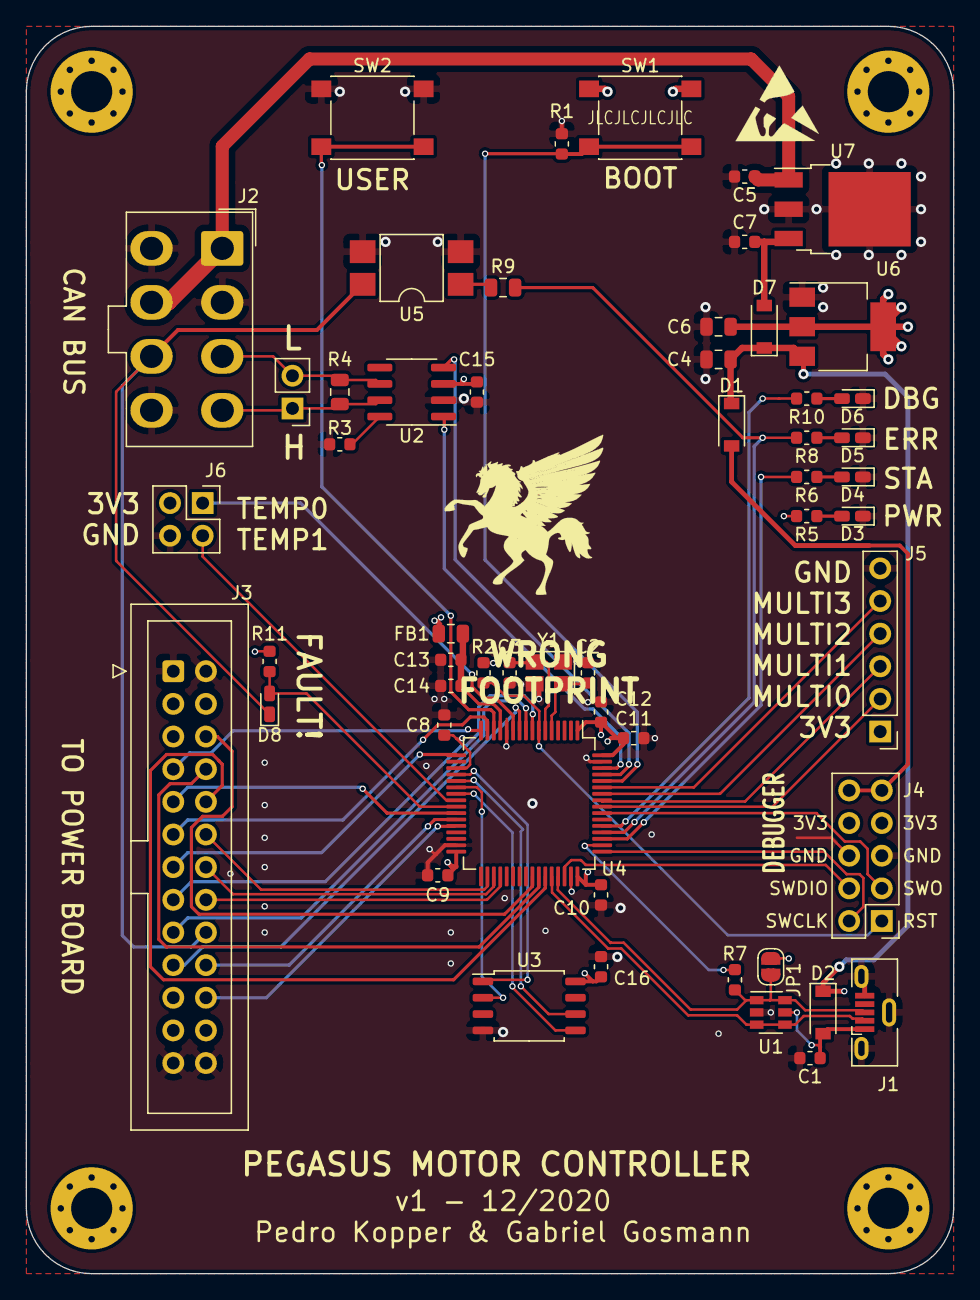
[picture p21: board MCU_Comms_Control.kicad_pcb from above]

Board: 4 copper layers, 72.1 x 97.0 mm, 54 parts (0 on the bottom side), 59 nets.

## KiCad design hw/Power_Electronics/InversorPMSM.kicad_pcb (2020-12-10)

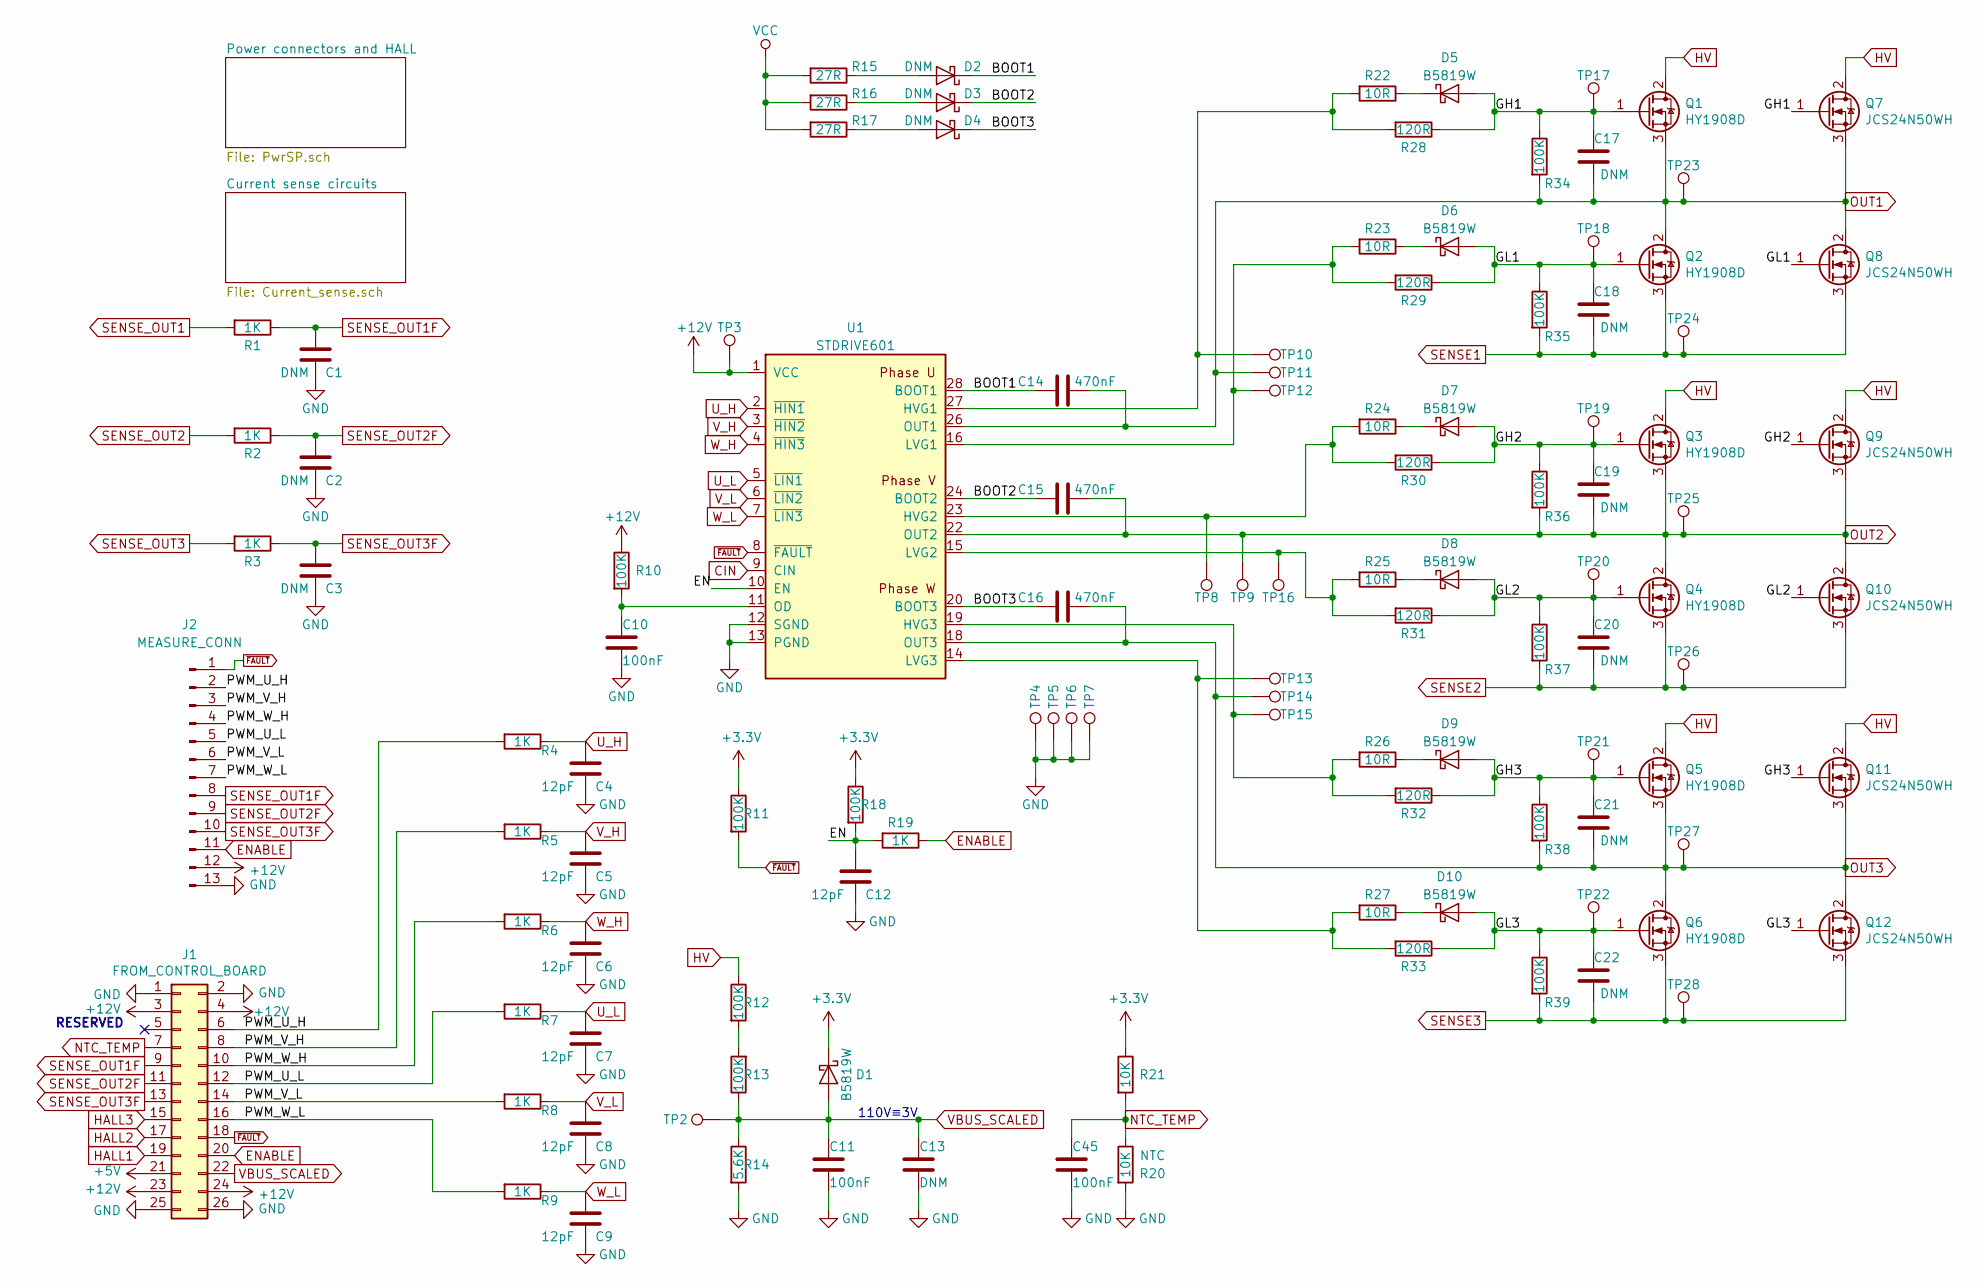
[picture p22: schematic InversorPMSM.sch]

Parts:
C1, C2, C3, C13, C17, C18, C19, C20, C21, C22: DNM; C_0603_1608Metric
C4, C5, C6, C7, C8, C9, C12: 12pF; C_0603_1608Metric; LCSC C38523
C10, C11, C45: 100nF; C_0603_1608Metric; LCSC C14663
C14, C15, C16: 470nF; C_0603_1608Metric; LCSC C1623
D1, D5, D6, D7, D8, D9, D10: B5819W; D_SOD-123; LCSC C8598
D2, D3, D4: DNM; D_SOD-123
J1: FROM_CONTROL_BOARD; IDC-Header_2x13_P2.54mm_Vertical
J2: MEASURE_CONN; PinHeader_1x13_P2.54mm_Vertical
Q1, Q2, Q3, Q4, Q5, Q6: HY1908D; Universal_MOSFET_generic
Q7, Q8, Q9, Q10, Q11, Q12: JCS24N50WH
R1, R2, R3, R4, R5, R6, R7, R8, R9, R19: 1K; R_0603_1608Metric; LCSC C21190
R10, R11, R18, R34, R35, R36, R37, R38, R39: 100K; R_0603_1608Metric; LCSC C25803
R12, R13: 100K; R_0805_2012Metric; LCSC C17407
R14: 5.6K; R_0805_2012Metric; LCSC C4382
R15, R16, R17: 27R; R_0603_1608Metric; LCSC C25190
R20: 10K; R_0603_1608Metric; LCSC C13564
R21: 10K; R_0603_1608Metric; LCSC C25804
R22, R23, R24, R25, R26, R27: 10R; R_0603_1608Metric; LCSC C22859
R28, R29, R30, R31, R32, R33: 120R; R_0603_1608Metric; LCSC C17437
TP2, TP3, TP4, TP5, TP6, TP7, TP8, TP9, TP10, TP11, TP12, TP13, TP14, TP15, TP16, TP17, TP18, TP19, TP20, TP21, TP22, TP23, TP24, TP25, TP26, TP27, TP28: TestPoint; TestPoint_Pad_D1.5mm
U1: STDRIVE601; SOIC-28W_7.5x17.9mm_P1.27mm

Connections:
+3V3: D1.1 (K), R11.1, R18.1, R21.1; also elsewhere on the board
+5V: J1.21; also elsewhere on the board
+12V: J1.3, J1.4, J1.23, J1.24, J2.12, R10.1, TP3.1, U1.1 (VCC); also elsewhere on the board
/BOOT1: C14.1, D2.1 (K), U1.28 (BOOT1)
/BOOT2: C15.1, D3.1 (K), U1.24 (BOOT2)
/BOOT3: C16.1, D4.1 (K), U1.20 (BOOT3)
/EN: C12.1, R18.2, R19.2, U1.10 (EN)
/GH1: C17.2, D5.2 (A), Q1.1 (G), Q7.1 (G), R28.1, R34.1, TP17.1
/GH2: C19.2, D7.2 (A), Q3.1 (G), Q9.1 (G), R30.1, R36.1, TP19.1
/GH3: C21.2, D9.2 (A), Q5.1 (G), Q11.1 (G), R32.1, R38.1, TP21.1
/GL1: C18.2, D6.2 (A), Q2.1 (G), Q8.1 (G), R29.1, R35.1, TP18.1
/GL2: C20.2, D8.2 (A), Q4.1 (G), Q10.1 (G), R31.1, R37.1, TP20.1
/GL3: C22.2, D10.2 (A), Q6.1 (G), Q12.1 (G), R33.1, R39.1, TP22.1
/PWM_U_H: J1.6, J2.2, R4.2
/PWM_U_L: J1.12, J2.5, R7.2
/PWM_V_H: J1.8, J2.3, R5.2
/PWM_V_L: J1.14, J2.6, R8.2
/PWM_W_H: J1.10, J2.4, R6.2
/PWM_W_L: J1.16, J2.7, R9.2
CIN: U1.9 (CIN); also elsewhere on the board
ENABLE: J1.20, J2.11, R19.1
GND: C1.2, C2.2, C3.2, C4.2, C5.2, C6.2, C7.2, C8.2, C9.2, C10.2, C11.2, C12.2, C13.2, C45.2, J1.1, J1.2, J1.25, J1.26, J2.13, R14.2, R20.2, TP4.1, TP5.1, TP6.1, TP7.1, U1.12 (SGND), U1.13 (PGND); also elsewhere on the board
HALL1: J1.19; also elsewhere on the board
HALL2: J1.17; also elsewhere on the board
HALL3: J1.15; also elsewhere on the board
HV: Q1.2 (D), Q3.2 (D), Q5.2 (D), Q7.2 (D), Q9.2 (D), Q11.2 (D), R12.1; also elsewhere on the board
NTC_TEMP: C45.1, J1.7, R20.1, R21.2
unnamed: C10.1, R10.2, U1.11 (OD)
unnamed: D2.2 (A), R15.1
unnamed: D3.2 (A), R16.1
unnamed: D4.2 (A), R17.1
unnamed: D5.1 (K), R22.1
unnamed: D6.1 (K), R23.1
unnamed: D7.1 (K), R24.1
unnamed: D8.1 (K), R25.1
unnamed: D9.1 (K), R26.1
unnamed: D10.1 (K), R27.1
unnamed: R12.2, R13.2
unnamed: R22.2, R28.2, TP10.1, U1.27 (HVG1)
unnamed: R23.2, R29.2, TP12.1, U1.16 (LVG1)
unnamed: R24.2, R30.2, TP8.1, U1.23 (HVG2)
unnamed: R25.2, R31.2, TP16.1, U1.15 (LVG2)
unnamed: R26.2, R32.2, TP15.1, U1.19 (HVG3)
unnamed: R27.2, R33.2, TP13.1, U1.14 (LVG3)
OUT1: C14.2, C17.1, Q1.3 (S), Q2.2 (D), Q7.3 (S), Q8.2 (D), R34.2, TP11.1, TP23.1, U1.26 (OUT1); also elsewhere on the board
OUT2: C15.2, C19.1, Q3.3 (S), Q4.2 (D), Q9.3 (S), Q10.2 (D), R36.2, TP9.1, TP25.1, U1.22 (OUT2); also elsewhere on the board
OUT3: C16.2, C21.1, Q5.3 (S), Q6.2 (D), Q11.3 (S), Q12.2 (D), R38.2, TP14.1, TP27.1, U1.18 (OUT3); also elsewhere on the board
SENSE1: C18.1, Q2.3 (S), Q8.3 (S), R35.2, TP24.1; also elsewhere on the board
SENSE2: C20.1, Q4.3 (S), Q10.3 (S), R37.2, TP26.1; also elsewhere on the board
SENSE3: C22.1, Q6.3 (S), Q12.3 (S), R39.2, TP28.1; also elsewhere on the board
SENSE_OUT1: R1.2; also elsewhere on the board
SENSE_OUT1F: C1.1, J1.9, J2.8, R1.1
SENSE_OUT2: R2.2; also elsewhere on the board
SENSE_OUT2F: C2.1, J1.11, J2.9, R2.1
SENSE_OUT3: R3.2; also elsewhere on the board
SENSE_OUT3F: C3.1, J1.13, J2.10, R3.1
U_H: C4.1, R4.1, U1.2 (~HIN1)
U_L: C7.1, R7.1, U1.5 (~LIN1)
VBUS_SCALED: C11.1, C13.1, D1.2 (A), J1.22, R13.1, R14.1, TP2.1
VCC: R15.2, R16.2, R17.2
V_H: C5.1, R5.1, U1.3 (~HIN2)
V_L: C8.1, R8.1, U1.6 (~LIN2)
W_H: C6.1, R6.1, U1.4 (~HIN3)
W_L: C9.1, R9.1, U1.7 (~LIN3)
~FAULT: J1.18, J2.1, R11.2, U1.8 (~FAULT)

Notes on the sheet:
RESERVED
110V≡3V

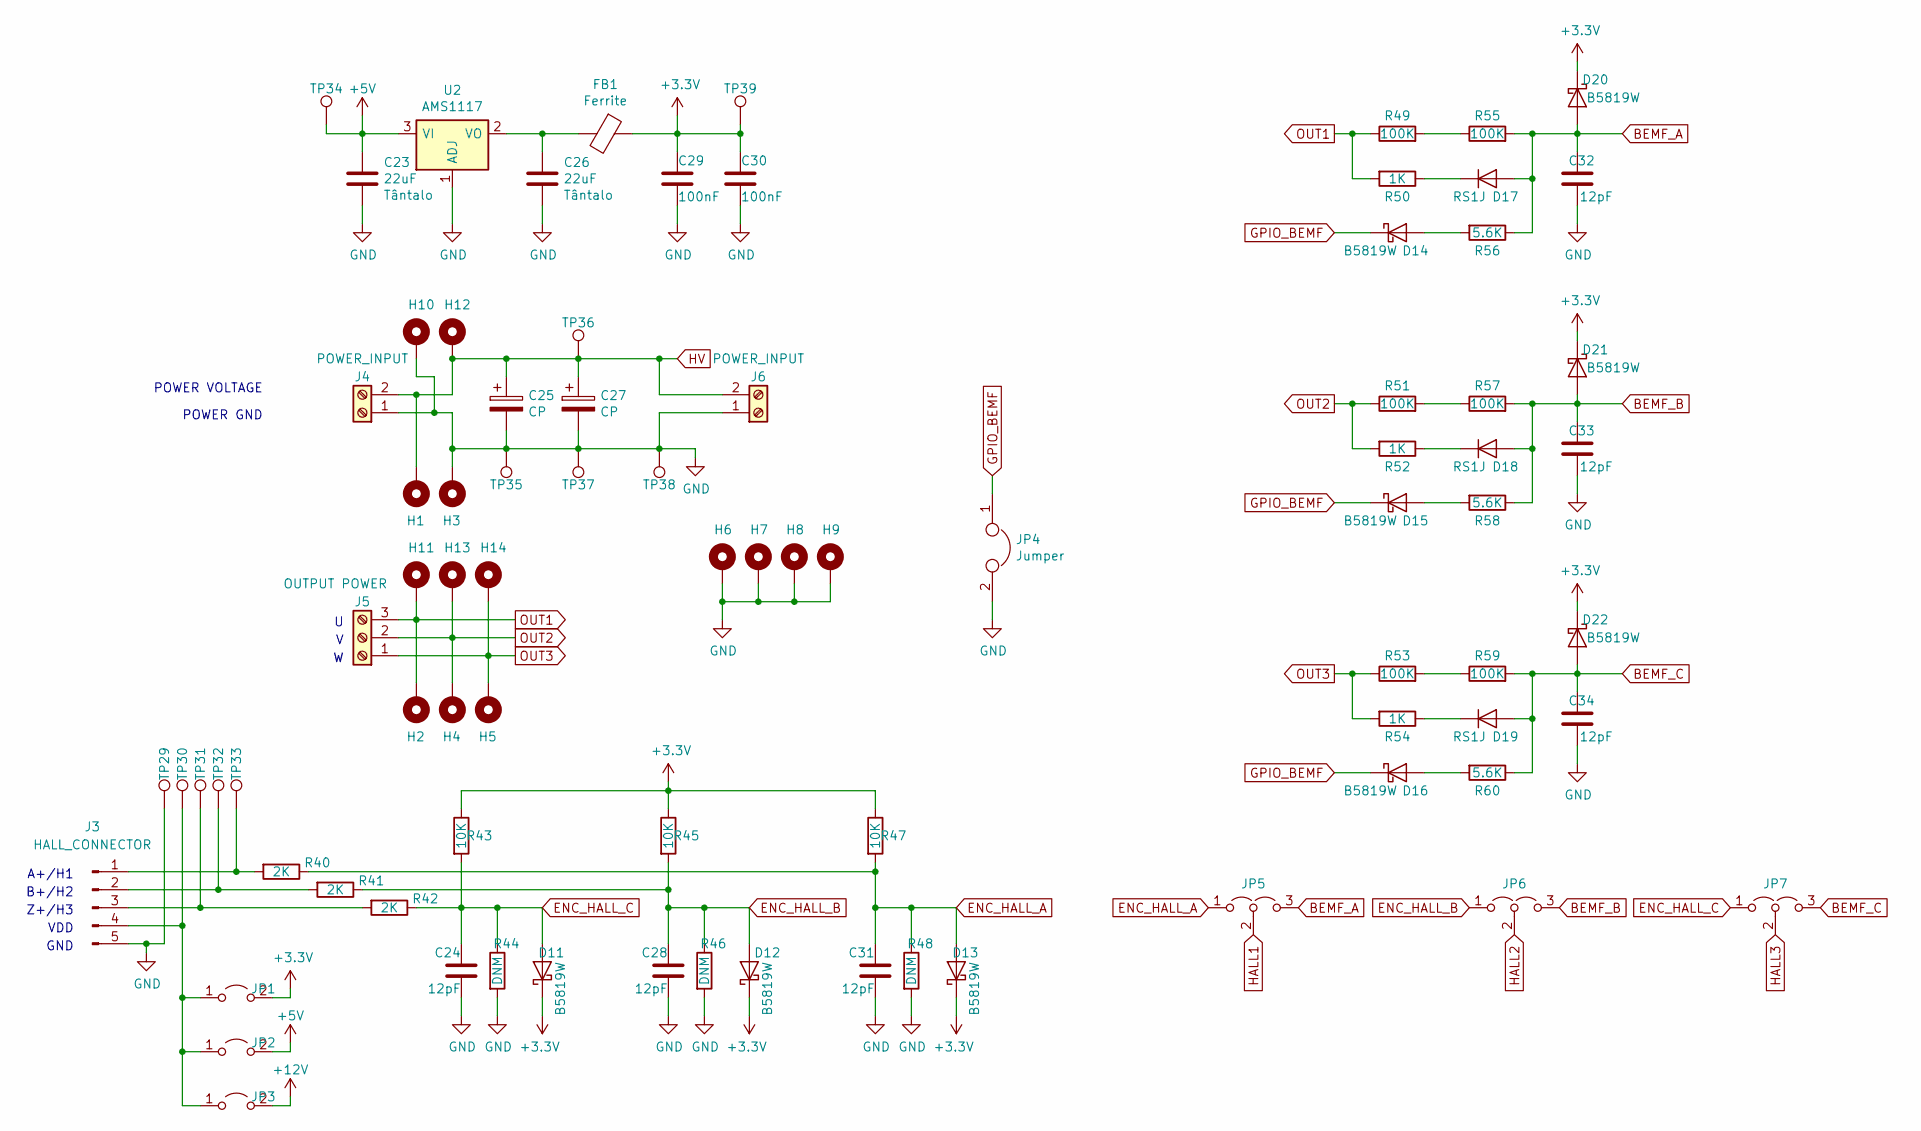
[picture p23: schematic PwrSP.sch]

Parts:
C23, C26: 22uF; C_0805_2012Metric; LCSC C45783
C24, C28, C31, C32, C33, C34: 12pF; C_0603_1608Metric; LCSC C38523
C25, C27: CP; CP_Radial_D18.0mm_P7.50mm_universal
C29, C30: 100nF; C_0603_1608Metric; LCSC C14663
D11, D12, D13, D14, D15, D16, D20, D21, D22: B5819W; D_SOD-123; LCSC C8598
D17, D18, D19: RS1J; D_SMA_custom; LCSC C169477
FB1: Ferrite; L_0805_2012Metric; LCSC C21189
H1, H2, H3, H4, H5: MountingHole_Pad; MountingHole_3.4mm_M3_Pad_Via
H6, H7, H8, H9: MountingHole_Pad; MountingHole_3.2mm_M3_Pad_Via
H10, H11, H12, H13, H14: MountingHole_Pad; MountingHole_2.2mm_M2_DIN965_Pad
J3: HALL_CONNECTOR; PinHeader_1x05_P2.54mm_Vertical
J4: POWER_INPUT
J5: OUTPUT POWER
J6: POWER_INPUT; Amass_XT60PW-M_Kombifootprint
JP1, JP2, JP3: Jumper_2_Open; SolderJumper-2_P1.3mm_Open_TrianglePad1.0x1.5mm
JP4: Jumper; SolderJumper-2_P1.3mm_Open_TrianglePad1.0x1.5mm
JP5, JP6, JP7: Jumper_3_Open; SolderJumper-3_P2.0mm_Open_TrianglePad1.0x1.5mm_custom
R40, R41, R42: 2K; R_0603_1608Metric; LCSC C22975
R43, R45, R47: 10K; R_0603_1608Metric; LCSC C25804
R44, R46, R48: DNM; R_0603_1608Metric
R49, R51, R53, R55, R57, R59: 100K; R_0805_2012Metric; LCSC C17407
R50, R52, R54: 1K; R_0603_1608Metric; LCSC C21190
R56, R58, R60: 5.6K; R_0805_2012Metric; LCSC C4382
TP29, TP30, TP31, TP32, TP33, TP34, TP35, TP36, TP37, TP38, TP39: TestPoint; TestPoint_Pad_D1.5mm
U2: AMS1117; SOT-223-3_TabPin2

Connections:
+3V3: C29.1, C30.1, D11.1 (K), D12.1 (K), D13.1 (K), D20.1 (K), D21.1 (K), D22.1 (K), FB1.1, JP1.2 (B), R43.1, R45.1, R47.1, TP39.1; also elsewhere on the board
+5V: C23.1, JP2.2 (B), TP34.1, U2.3 (VI); also elsewhere on the board
+12V: JP3.2 (B); also elsewhere on the board
BEMF_A: C32.2, D17.2 (A), D20.2 (A), JP5.3 (B), R55.2, R56.1
BEMF_B: C33.2, D18.2 (A), D21.2 (A), JP6.3 (B), R57.2, R58.1
BEMF_C: C34.2, D19.2 (A), D22.2 (A), JP7.3 (B), R59.2, R60.1
ENC_HALL_A: C31.2, D13.2 (A), JP5.1 (A), R40.1, R47.2, R48.1
ENC_HALL_B: C28.2, D12.2 (A), JP6.1 (A), R41.1, R45.2, R46.1
ENC_HALL_C: C24.2, D11.2 (A), JP7.1 (A), R42.1, R43.2, R44.1
GND: C23.2, C24.1, C25.2, C26.2, C27.2, C28.1, C29.2, C30.2, C31.1, C32.1, C33.1, C34.1, H3.1, H6.1, H7.1, H8.1, H9.1, H10.1, J3.5, J4.1, J6.1, JP4.2, R44.2, R46.2, R48.2, TP29.1, TP35.1, TP37.1, TP38.1, U2.1 (ADJ); also elsewhere on the board
GPIO_BEMF: D14.1 (K), D15.1 (K), D16.1 (K), JP4.1
HALL1: JP5.2 (C); also elsewhere on the board
HALL2: JP6.2 (C); also elsewhere on the board
HALL3: JP7.2 (C); also elsewhere on the board
HV: C25.1, C27.1, H1.1, H12.1, J4.2, J6.2, TP36.1; also elsewhere on the board
unnamed: C26.1, FB1.2, U2.2 (VO)
unnamed: D14.2 (A), R56.2
unnamed: D15.2 (A), R58.2
unnamed: D16.2 (A), R60.2
unnamed: D17.1 (K), R50.1
unnamed: D18.1 (K), R52.1
unnamed: D19.1 (K), R54.1
unnamed: J3.1, R40.2, TP33.1
unnamed: J3.2, R41.2, TP32.1
unnamed: J3.3, R42.2, TP31.1
unnamed: J3.4, JP1.1 (A), JP2.1 (A), JP3.1 (A), TP30.1
unnamed: R49.2, R55.1
unnamed: R51.2, R57.1
unnamed: R53.2, R59.1
OUT1: H2.1, H11.1, J5.3, R49.1, R50.2; also elsewhere on the board
OUT2: H4.1, H13.1, J5.2, R51.1, R52.2; also elsewhere on the board
OUT3: H5.1, H14.1, J5.1, R53.1, R54.2; also elsewhere on the board

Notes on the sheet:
POWER VOLTAGE
POWER GND
A+/H1
B+/H2
Z+/H3
GND
VDD

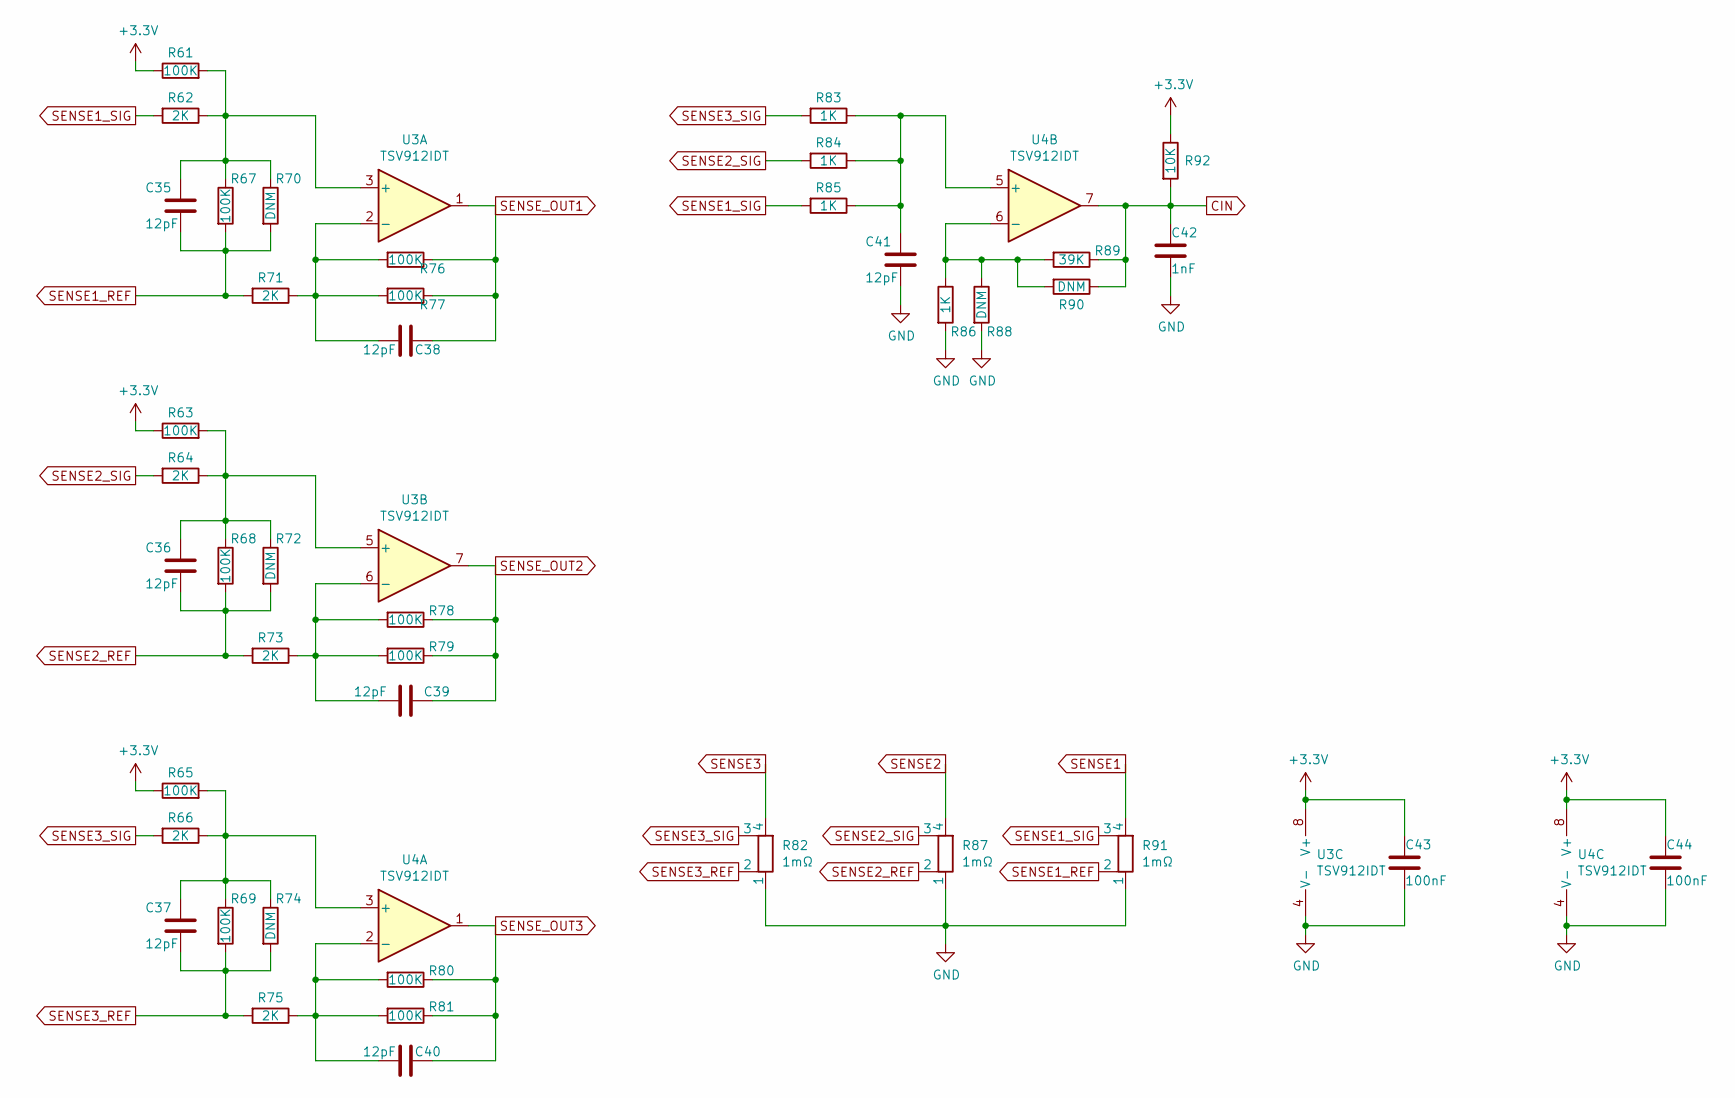
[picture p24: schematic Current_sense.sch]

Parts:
C35, C36, C37, C38, C39, C40, C41: 12pF; C_0603_1608Metric; LCSC C38523
C42: 1nF; C_0603_1608Metric
C43, C44: 100nF; C_0603_1608Metric; LCSC C14663
R61, R63, R65, R67, R68, R69, R76, R77, R78, R79, R80, R81: 100K; R_0603_1608Metric; LCSC C25803
R62, R64, R66, R71, R73, R75: 2K; R_0603_1608Metric; LCSC C22975
R70, R72, R74, R88, R90: DNM; R_0603_1608Metric
R82, R87, R91: 1mΩ; R_2512_6332Metric
R83, R84, R85, R86: 1K; R_0603_1608Metric; LCSC C21190
R89: 39K; R_0603_1608Metric; LCSC C23153
R92: 10K; R_0603_1608Metric; LCSC C25804
U3, U4: TSV912IDT; SOIC-8_3.9x4.9mm_P1.27mm

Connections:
+3V3: C43.1, C44.1, R61.1, R63.1, R65.1, R92.1, U3.8 (V+), U4.8 (V+); also elsewhere on the board
CIN: C42.1, R89.1, R90.1, R92.2, U4.7; also elsewhere on the board
GND: C41.2, C42.2, C43.2, C44.2, R82.1, R86.2, R87.1, R88.2, R91.1, U3.4 (V-), U4.4 (V-); also elsewhere on the board
unnamed: C35.1, R61.2, R62.1, R67.1, R70.1, U3.3 (+)
unnamed: C36.1, R63.2, R64.1, R68.1, R72.1, U3.5 (+)
unnamed: C37.1, R65.2, R66.1, R69.1, R74.1, U4.3 (+)
unnamed: C38.1, R71.1, R76.2, R77.2, U3.2 (-)
unnamed: C39.1, R73.1, R78.2, R79.2, U3.6 (-)
unnamed: C40.1, R75.1, R80.2, R81.2, U4.2 (-)
unnamed: C41.1, R83.1, R84.1, R85.1, U4.5 (+)
unnamed: R86.1, R88.1, R89.2, R90.2, U4.6 (-)
SENSE1: R91.4; also elsewhere on the board
SENSE1_REF: C35.2, R67.2, R70.2, R71.2, R91.2
SENSE1_SIG: R62.2, R85.2, R91.3
SENSE2: R87.4; also elsewhere on the board
SENSE2_REF: C36.2, R68.2, R72.2, R73.2, R87.2
SENSE2_SIG: R64.2, R84.2, R87.3
SENSE3: R82.4; also elsewhere on the board
SENSE3_REF: C37.2, R69.2, R74.2, R75.2, R82.2
SENSE3_SIG: R66.2, R82.3, R83.2
SENSE_OUT1: C38.2, R76.1, R77.1, U3.1; also elsewhere on the board
SENSE_OUT2: C39.2, R78.1, R79.1, U3.7; also elsewhere on the board
SENSE_OUT3: C40.2, R80.1, R81.1, U4.1; also elsewhere on the board

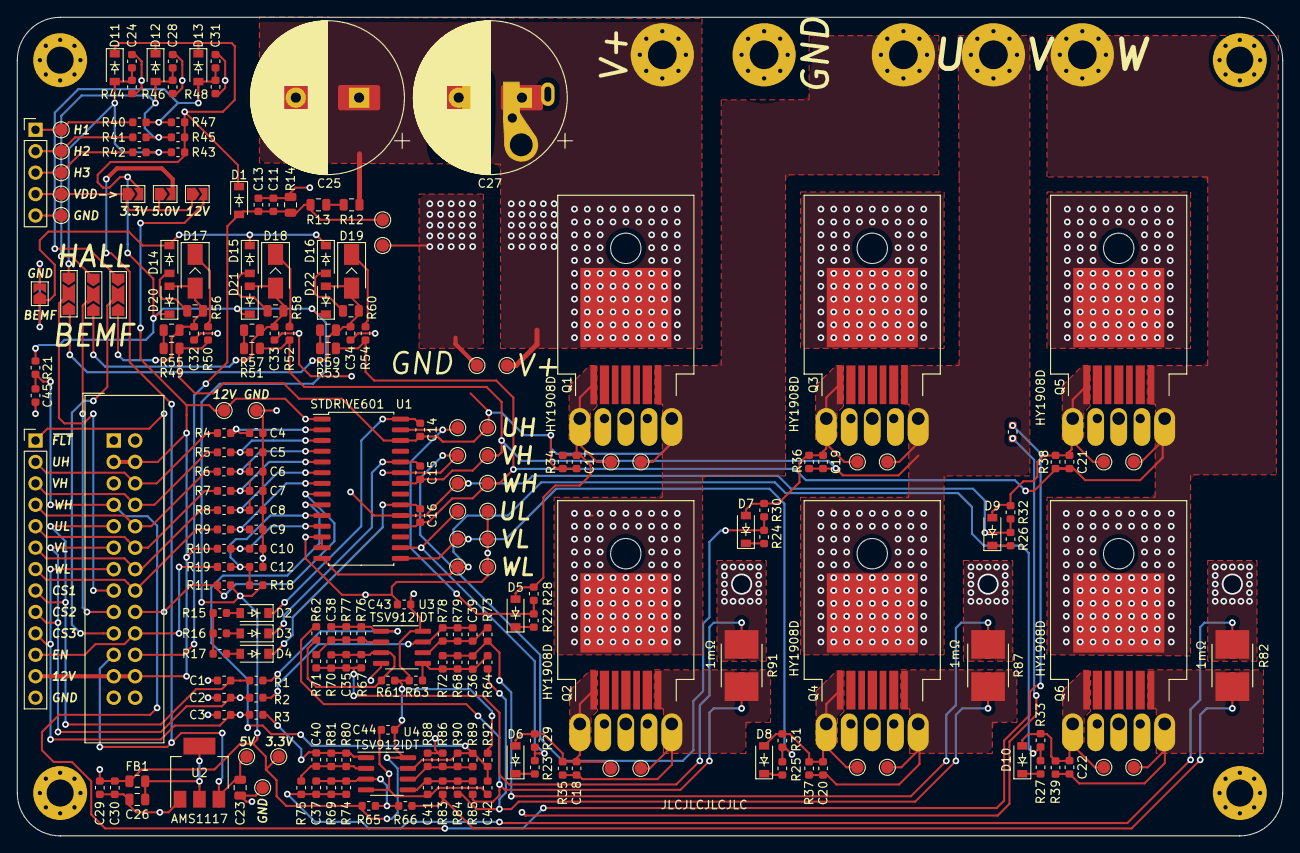
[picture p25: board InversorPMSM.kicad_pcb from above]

Board: 2 copper layers, 150.0 x 97.0 mm, 228 parts (0 on the bottom side), 100 nets.

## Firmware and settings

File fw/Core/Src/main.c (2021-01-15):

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

/* Includes ------------------------------------------------------------------*/
#include "main.h"
#include "adc.h"
#include "can.h"
#include "spi.h"
#include "tim.h"
#include "usart.h"
#include "usb.h"
#include "gpio.h"

/* USER CODE BEGIN Includes */
#include <stdio.h>
#include <string.h>
/* USER CODE END Includes */


void SystemClock_Config(void);
/**
  * @brief  The application entry point.
  * @retval int
  */
int main(void)
{
  

  /* MCU Configuration--------------------------------------------------------*/

  /* Reset of all peripherals, Initializes the Flash interface and the Systick. */
  HAL_Init();

  /* Configure the system clock */
  SystemClock_Config();

  /* Initialize all configured peripherals */
  MX_GPIO_Init();
  MX_ADC1_Init();
  MX_ADC2_Init();
  MX_ADC3_Init();
  MX_CAN_Init();
  MX_SPI1_Init();
  MX_TIM1_Init();
  MX_USART1_UART_Init();
  MX_USB_PCD_Init();
  /* USER CODE BEGIN 2 */

  // Testa o funcionamento da flash
  // Acaba também testando a UART (MULTI2/3)
  uint8_t tx_buf[] = { 0x9F, 0x00, 0x00, 0x00, 0x00 };
  uint8_t rx_buf[5] = {0};
  HAL_GPIO_WritePin(FLASH_CS_GPIO_Port, FLASH_CS_Pin, SET);
  HAL_Delay(10);
  HAL_GPIO_WritePin(FLASH_CS_GPIO_Port, FLASH_CS_Pin, RESET);
  HAL_SPI_TransmitReceive(&hspi1, tx_buf, rx_buf, sizeof(rx_buf), 0xff);
  HAL_GPIO_WritePin(FLASH_CS_GPIO_Port, FLASH_CS_Pin, SET);
  uint32_t serial = rx_buf[1] << 16 | rx_buf[2] << 8 | rx_buf[3];

  char buf[200];
  sprintf(buf, "---\r\nFlash Serial: %lu | %s\n\r ", serial, serial == 15679512 ? "PASS" : "FAIL");
  HAL_UART_Transmit(&huart1, (uint8_t *) buf, strlen(buf), 0xff);

  /* USER CODE END 2 */
 
 

  /* Infinite loop */
  /* USER CODE BEGIN WHILE */
  while (1)
  {
	  // Testa os LEDs
	  HAL_GPIO_TogglePin(STATUS_GPIO_Port, STATUS_Pin);
	  HAL_GPIO_TogglePin(ERR_OUT_GPIO_Port, ERR_OUT_Pin);
	  HAL_GPIO_TogglePin(DEBUG_LED_GPIO_Port, DEBUG_LED_Pin);
	  HAL_Delay(500);
	  HAL_GPIO_TogglePin(STATUS_GPIO_Port, STATUS_Pin);
	  HAL_GPIO_TogglePin(ERR_OUT_GPIO_Port, ERR_OUT_Pin);
	  HAL_GPIO_TogglePin(DEBUG_LED_GPIO_Port, DEBUG_LED_Pin);
	  HAL_Delay(500);

    /* USER CODE END WHILE */

    /* USER CODE BEGIN 3 */
  }
  /* USER CODE END 3 */
}

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


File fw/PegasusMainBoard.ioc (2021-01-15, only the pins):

Mcu.UserName=STM32F303RCTx
PA0.GPIO_Label=USER_BUTTON
PA0.Signal=GPIO_Input
PA1.GPIO_Label=CURR_V
PA1.Signal=ADC1_IN2
PA10.GPIO_Label=W_H
PA10.Signal=S_TIM1_CH3
PA11.Signal=USB_DM
PA12.Signal=USB_DP
PA13.Signal=SYS_JTMS-SWDIO
PA14.Signal=SYS_JTCK-SWCLK
PA2.GPIO_Label=NTC_PWR
PA2.Signal=ADC1_IN3
PA3.GPIO_Label=CURR_W
PA3.Signal=ADC1_IN4
PA4.GPIO_Label=FLASH_CS
PA4.Signal=GPIO_Output
PA5.GPIO_Label=FLASH_CLK
PA5.Signal=SPI1_SCK
PA6.GPIO_Label=FLASH_MISO
PA6.Signal=SPI1_MISO
PA7.GPIO_Label=FLASH_MOSI
PA7.Signal=SPI1_MOSI
PA8.Signal=RCC_MCO
PA9.GPIO_Label=V_H
PA9.Signal=S_TIM1_CH2
PB0.GPIO_Label=CURR_U
PB0.Signal=ADC3_IN12
PB1.GPIO_Label=PWR_ENABLE
PB1.Signal=GPIO_Output
PB13.GPIO_Label=U_L
PB13.Signal=TIM1_CH1N
PB14.GPIO_Label=V_L
PB14.Signal=TIM1_CH2N
PB15.GPIO_Label=W_L
PB15.Signal=TIM1_CH3N
PB2.GPIO_Label=VBUS_SCALED
PB2.Signal=ADC2_IN12
PB3.Signal=SYS_JTDO-TRACESWO
PB4.GPIO_Label=MULTI0
PB4.Signal=GPIO_Input
PB5.GPIO_Label=MULTI1
PB5.Signal=GPIO_Input
PB6.GPIO_Label=MULTI2_TX
PB6.Signal=USART1_TX
PB7.GPIO_Label=MULTI3_RX
PB7.Signal=USART1_RX
PB8.Signal=CAN_RX
PB9.Signal=CAN_TX
PC0.GPIO_Label=HALL3
PC0.Signal=GPIO_Input
PC1.GPIO_Label=HALL2
PC1.Signal=GPIO_Input
PC10.GPIO_Label=STATUS
PC10.Signal=GPIO_Output
PC11.GPIO_Label=ERR_OUT
PC11.Signal=GPIO_Output
PC12.GPIO_Label=DEBUG_LED
PC12.Signal=GPIO_Output
PC2.GPIO_Label=HALL1
PC2.Signal=GPIO_Input
PC3.GPIO_Label=TEMP0
PC3.Signal=ADCx_IN9
PC4.GPIO_Label=TEMP1
PC4.Signal=ADC2_IN5
PC5.GPIO_Label=ERR_IN
PC5.Signal=ADC2_IN11
PF0-OSC_IN.Signal=RCC_OSC_IN
PF1-OSC_OUT.Signal=RCC_OSC_OUT

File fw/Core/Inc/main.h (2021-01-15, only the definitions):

#define HALL3_Pin GPIO_PIN_0
#define HALL3_GPIO_Port GPIOC
#define HALL2_Pin GPIO_PIN_1
#define HALL2_GPIO_Port GPIOC
#define HALL1_Pin GPIO_PIN_2
#define HALL1_GPIO_Port GPIOC
#define TEMP0_Pin GPIO_PIN_3
#define TEMP0_GPIO_Port GPIOC
#define USER_BUTTON_Pin GPIO_PIN_0
#define USER_BUTTON_GPIO_Port GPIOA
#define CURR_V_Pin GPIO_PIN_1
#define CURR_V_GPIO_Port GPIOA
#define NTC_PWR_Pin GPIO_PIN_2
#define NTC_PWR_GPIO_Port GPIOA
#define CURR_W_Pin GPIO_PIN_3
#define CURR_W_GPIO_Port GPIOA
#define FLASH_CS_Pin GPIO_PIN_4
#define FLASH_CS_GPIO_Port GPIOA
#define FLASH_CLK_Pin GPIO_PIN_5
#define FLASH_CLK_GPIO_Port GPIOA
#define FLASH_MISO_Pin GPIO_PIN_6
#define FLASH_MISO_GPIO_Port GPIOA
#define FLASH_MOSI_Pin GPIO_PIN_7
#define FLASH_MOSI_GPIO_Port GPIOA
#define TEMP1_Pin GPIO_PIN_4
#define TEMP1_GPIO_Port GPIOC
#define ERR_IN_Pin GPIO_PIN_5
#define ERR_IN_GPIO_Port GPIOC
#define CURR_U_Pin GPIO_PIN_0
#define CURR_U_GPIO_Port GPIOB
#define PWR_ENABLE_Pin GPIO_PIN_1
#define PWR_ENABLE_GPIO_Port GPIOB
#define VBUS_SCALED_Pin GPIO_PIN_2
#define VBUS_SCALED_GPIO_Port GPIOB
#define U_L_Pin GPIO_PIN_13
#define U_L_GPIO_Port GPIOB
#define V_L_Pin GPIO_PIN_14
#define V_L_GPIO_Port GPIOB
#define W_L_Pin GPIO_PIN_15
#define W_L_GPIO_Port GPIOB
#define V_H_Pin GPIO_PIN_9
#define V_H_GPIO_Port GPIOA
#define W_H_Pin GPIO_PIN_10
#define W_H_GPIO_Port GPIOA
#define STATUS_Pin GPIO_PIN_10
#define STATUS_GPIO_Port GPIOC
#define ERR_OUT_Pin GPIO_PIN_11
#define ERR_OUT_GPIO_Port GPIOC
#define DEBUG_LED_Pin GPIO_PIN_12
#define DEBUG_LED_GPIO_Port GPIOC
#define MULTI0_Pin GPIO_PIN_4
#define MULTI0_GPIO_Port GPIOB
#define MULTI1_Pin GPIO_PIN_5
#define MULTI1_GPIO_Port GPIOB
#define MULTI2_TX_Pin GPIO_PIN_6
#define MULTI2_TX_GPIO_Port GPIOB
#define MULTI3_RX_Pin GPIO_PIN_7
#define MULTI3_RX_GPIO_Port GPIOB

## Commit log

2020-11-12 estrutura basica
    [InversorPMSM.kicad_pcb, InversorPMSM.sch]
2020-11-16 Start working on digital board
    [MCU_Comms_Control.sch, PwrSD.sch]
2020-11-18 continue digital design
    [MCU_Comms_Control.sch, PwrSD.sch]
2020-11-18 finish schematic of mcu/comms and start review process
    [MCU_Comms_Control.sch, PwrSD.sch]
2020-11-21 add footprints and lcsc code
    [MCU_Comms_Control.sch, PwrSD.sch]
2020-11-21 start drawing schematic
    [MCU_Comms_Control.kicad_pcb, MCU_Comms_Control.sch]
2020-11-21 finish drawing schematic and add silkscreen
    [MCU_Comms_Control.kicad_pcb, MCU_Comms_Control.sch]
2020-11-22 footprint adjust
    [MCU_Comms_Control.kicad_pcb]
2020-11-27 add missing files
    [MCU_Comms_Control-B_Cu.gbr, MCU_Comms_Control-B_Mask.gbr, MCU_Comms_Control-B_Paste.gbr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]
2020-11-27 start power electronics schematic
    [InversorPMSM.kicad_pcb, InversorPMSM.sch, PwrSP.sch]
2020-12-01 advances were made on power electronics board
    [Current_sense.sch, InversorPMSM.kicad_pcb, InversorPMSM.sch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]
2020-12-01 update schematic with hall and BEMF circuits
    [Current_sense.sch, InversorPMSM.sch, PwrSP.sch]
2020-12-02 all component's positions are more or less defined
    [Current_sense.sch, InversorPMSM.kicad_pcb, InversorPMSM.sch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]
2020-12-03 further advances made on the layout
    [InversorPMSM.kicad_pcb]
2020-12-06 finish power board layout first pass
    [InversorPMSM.kicad_pcb, PwrSD.sch]
2020-12-06 adjustments made on silkscreen layer
    [Current_sense.sch, InversorPMSM.kicad_pcb, InversorPMSM.sch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]
2020-12-08 turn power electronics PCB into a 2 layer board
    [InversorPMSM-B_Cu.gbr, InversorPMSM-B_Mask.gbr, InversorPMSM-B_Paste.gbr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]
2020-12-08 remove old gerbers and assembly files
    [MCU_Comms_Control-B_Cu.gbr, MCU_Comms_Control-B_Mask.gbr, MCU_Comms_Control-B_Paste.gbr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]
2020-12-08 new mcu board revision
2020-12-08 adjusts made on mask layer to expose high current path
    [Current_sense.sch, InversorPMSM.kicad_pcb, InversorPMSM.sch]
2020-12-09 update pour clearences
    [MCU_Comms_Control.kicad_pcb]
2020-12-09 create high voltage net class and solve DRC erros
    [Current_sense.sch, InversorPMSM.kicad_pcb, InversorPMSM.sch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]
2020-12-12 change stm32 to lfqp64 (schematic)
    [MCU_Comms_Control-B_Cu.gbr, MCU_Comms_Control-B_Mask.gbr, MCU_Comms_Control-B_Paste.gbr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]
2020-12-13 add lqfp64 board version
    [MCU_Comms_Control.kicad_pcb, MCU_Comms_Control_lqfp48.kicad_pcb]
2020-12-13 add pegasus to new board
2020-12-14 finish new control board revision
    [MCU_Comms_Control.kicad_pcb, MCU_Comms_Control.sch]
2020-12-14 specify order number location on pcb
    [MCU_Comms_Control.kicad_pcb]
2020-12-14 add colateral files of new design
    [MCU_Comms_Control-B_Cu.gbr, MCU_Comms_Control-B_Mask.gbr, MCU_Comms_Control-B_Paste.gbr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]
2020-12-14 add other colateral files of new design
    [MCU_Comms_Control.sch]
2021-01-14 fix boot0 resistor
    [MCU_Comms_Control.kicad_pcb, MCU_Comms_Control.sch]
2021-01-15 tag wrong crystal footprint
    [MCU_Comms_Control.kicad_pcb, MCU_Comms_Control.sch]
2021-05-25 mini-fit (CAN) connector hole size from 1.4 to 1.8mm diameter and add silkscreen labels for the debugger pins
    [MCU_Comms_Control.kicad_pcb, MCU_Comms_Control.sch]
2021-09-14 add power electronics renders
    [MCU_Comms_Control.sch]

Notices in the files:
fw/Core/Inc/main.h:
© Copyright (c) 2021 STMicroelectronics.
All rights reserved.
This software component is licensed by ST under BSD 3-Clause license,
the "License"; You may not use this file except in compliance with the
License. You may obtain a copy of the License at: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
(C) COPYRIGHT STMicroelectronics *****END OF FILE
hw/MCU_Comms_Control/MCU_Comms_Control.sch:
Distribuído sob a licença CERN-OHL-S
